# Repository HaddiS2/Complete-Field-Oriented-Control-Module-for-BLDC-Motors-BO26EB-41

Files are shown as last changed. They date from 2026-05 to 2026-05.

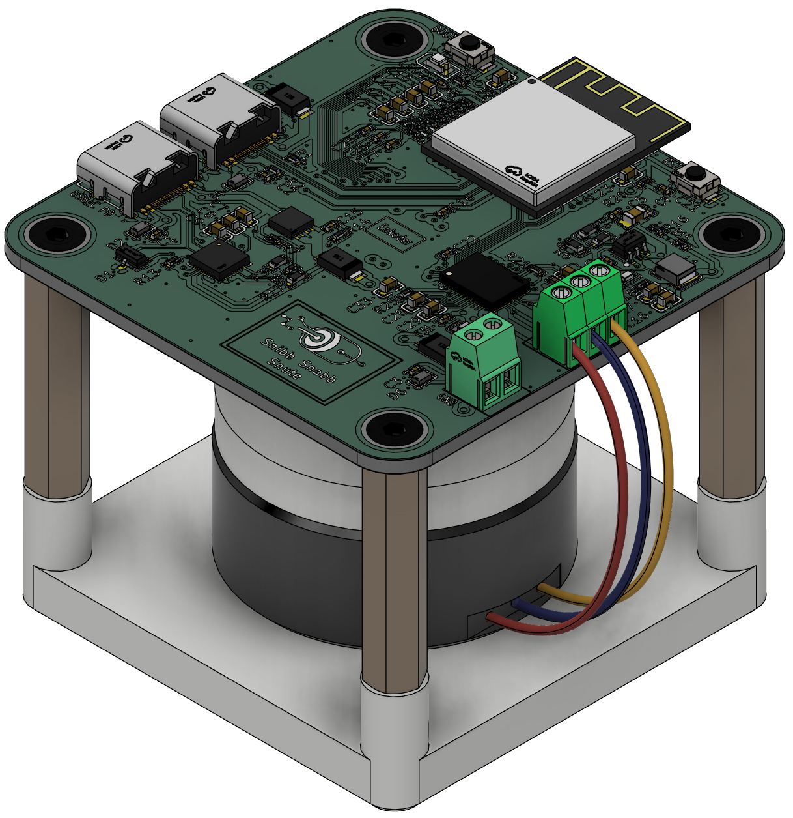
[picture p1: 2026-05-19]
CAD/FOC_Motor_Rig_Top_View.png

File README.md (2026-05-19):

# Complete-Field-Oriented-Control-Module-for-BLDC-Motors-BO26EB-41
Custom field-oriented control (FOC) motor controller with USB-C Power Delivery.

This repository contains the hardware design files, firmware, and test rig for a custom brushless motor controller built around field-oriented control (FOC). The board negotiates its supply voltage over USB-C Power Delivery using an STUSB4500, and measures rotor position with a TLE5009 magnetic encoder mounted directly beneath the motor shaft. The PCB was designed in KiCad, and a custom test rig — modeled in Fusion 360 and 3D printed — holds the motor and controller in fixed alignment to keep the encoder-to-magnet spacing constant for repeatable position- and velocity-control testing.

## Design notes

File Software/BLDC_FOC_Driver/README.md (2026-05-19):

# BLDC FOC Driver 
 
Motor controller based on Field Oriented Control (FOC). 
 
## Required Libraries: 
- **SimpleFOC** - Install via Arduino Library Manager 
- **SparkFun_STUSB4500** - Install via Arduino Library Manager (if needed) 
 
## Installation: 
1. Open Arduino IDE 
2. Go to **Sketch  Include Library  Manage Libraries** 
3. Search for "SimpleFOC" and install 
4. Search for "SparkFun STUSB4500" and install

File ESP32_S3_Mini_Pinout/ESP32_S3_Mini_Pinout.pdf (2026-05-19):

## ESP-32 S3 mini pin out diagram

Pin number | IO number | Pin type | Pin connection | description
1 | GND | GND | GND
2 | GND | GND | GND
3 | 3v3 | 3v3 | Powersupply3v3
4 | IO00 STRAPPING PIN | | Boot
5 | IO01 | ADC | Vref
6 | IO02 | ADC | ENK_Vgmr
7 | IO03 STRAPPING PIN | | -
8 | IO04 | ADC | ENK_SINN
9 | IO05 | ADC | ENK_SINP
10 | IO06 | ADC | ENK_COSP
11 | IO07 | ADC | ENK_COSN
12 | IO08 | ADC | SOA
13 | IO09 | ADC | SOB
14 | IO10 | ADC | SOC
15 | IO11 | IO | PWM_LC
16 | IO12 | IO | PWM_HC
17 | IO13 | IO | PWM_LB
18 | IO14 | IO | PWM_HB
19 | IO15 | IO | PWM_LA
20 | IO16 | IO | PWM_HA
21 | IO17 | I2C | SDA
22 | IO18 | I2C | SCL
23 | IO19 | D- | USB_C data | -
24 | IO20 | D+ | USB_C data | +
25 | IO21 | IO | RST_PDA
26 | IO26b | NC | -
27 | IO47 | SDA | SPICLK_P_DIFF
28 | IO33 | SPI/IO4 | SPI_nSCS
29 | IO34 | SPI/IO4 | SPI_SCLK
30 | IO48 | SDA | SPICLK_N_DIFF
31 | IO35 | SPI/IO6 | SPI_SDI
32 | IO36 | SPI/IO7 | SPI_SDO
33 | IO37 | SPI/IO | nSLEEP
34 | IO38 | IO | nFAULT
35 | IO39 | JTAG/IO | DRVOFF
36 | IO40 | JTAG | NC
37 | IO41 | JTAG | NC
38 | IO42 | JTAG | NC
39 | TXD0 | RTXDO | NC
40 | RXT0 | RXDO | NC
41 | IO45 STRAPPING PIN | | NC
44 | IO46 STRAPPING PIN | | NC
45 | EN | EN | NC
42,43,46,47,48 | - | GND | GND

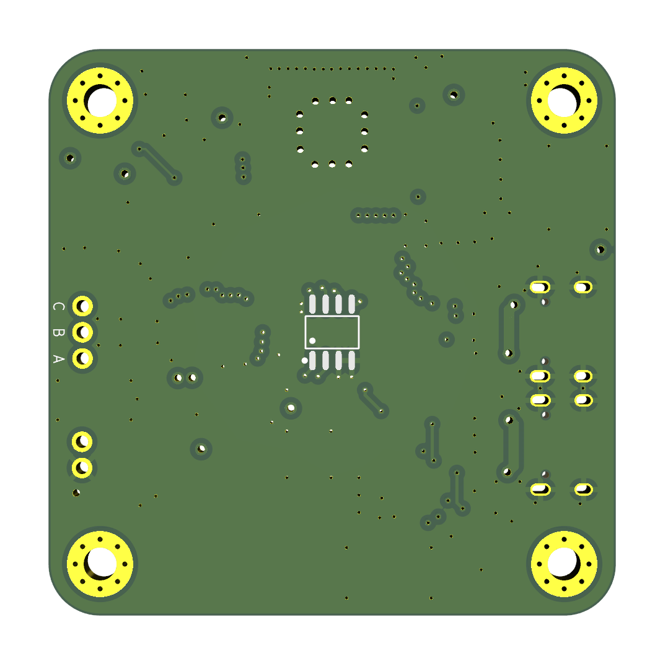
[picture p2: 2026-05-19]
Hardware/PCB_BackCompressed.png

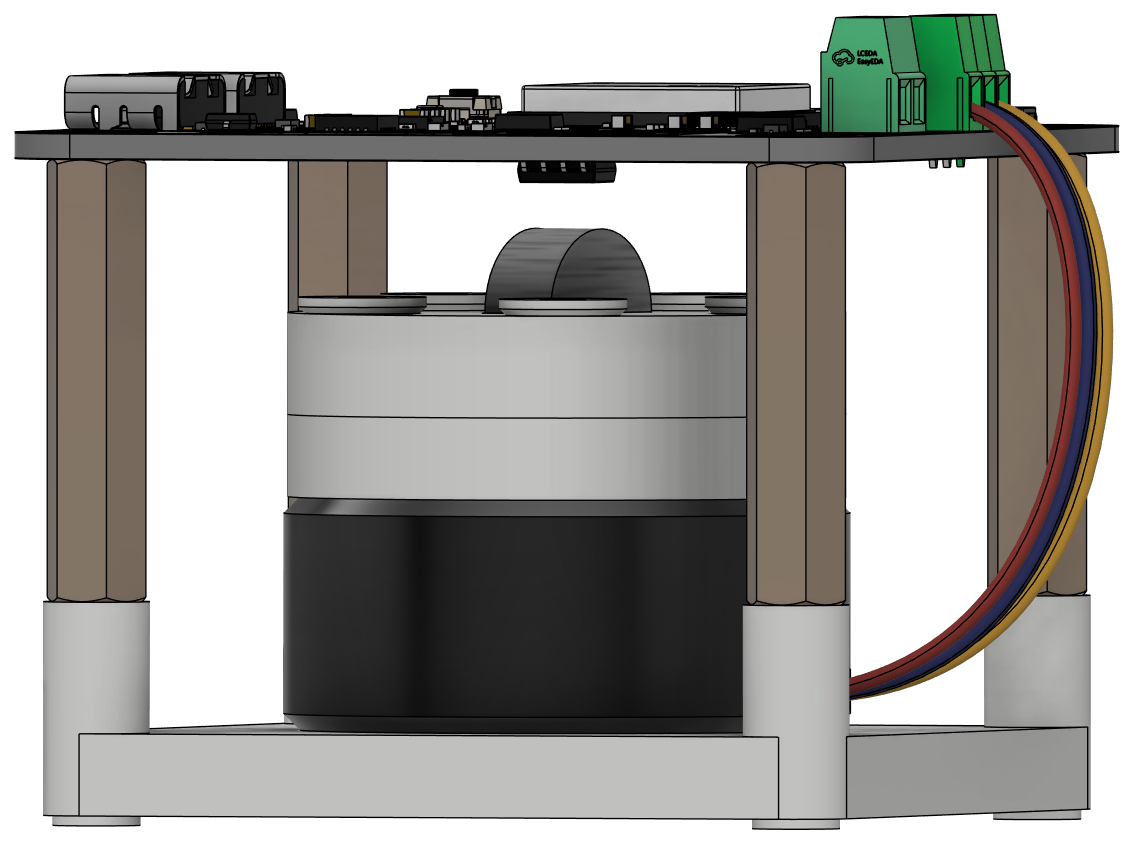
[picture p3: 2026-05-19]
CAD/FOC_Motor_Rig_Side_View.png

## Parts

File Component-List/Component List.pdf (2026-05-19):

1

# Component list for first iteration

Component | Description | Quantity | Electrical Specification | Size [SMD] | LCSC part# | Name | Component Link | Datasheet Link | Price x Qty Capacitor | CVM1/MCU_V | x10 | 100nF 50V X7R ±10% | 0603 | C14663 | CC0603KRX7R9BB104 | C14663 | C14663 | $0.0026 x 1 Capacitor | CVM2/VIN | x2 | 10uF 50V X7R ±10 | 1206 | C89632 | CL31B106KBHNNNE | C89632 | C89632 | $0.0377 x 1 Capacitor | CCP/CAVVD/MCU_EN/2.7/1.2/VDD | x6 | 1uF 50V X7R ±10% | 0805 | C28323 | CL21B105KBFNNNE | C28323 | C28323 | $0.0099 x 1 Capacitor | MCU_V/SW_BK/3V3/3V3 | x4 | 22uF 25V X5R ±20% | 0805 | C45783 | CL21A226MAQNNNE | C45783 | C45783 | $0.0308 x 1 Capacitor | CSOX | x3 | 22pF 50V C0G ±5% | 0402 | C1555 | CL21A226MAQNNNE | C1555 | C1555 | $0.0012 x 1 Capacitor | CFLY | x1 | 47nF 50V X7R ±10% | 0603 | C1622 | CL10B473KB8NNNC | C1622 | C1622 | $0.0052 x 1 Capacitor | SINP/SINN/COSP/COSN | x4 | 68nF 50V C0G ±5% | 1206 | C77084 | GRM31C5C1H683JA01L | C77084 | C77084 | $0.1122 x 1 Capacitor | GMR/VDD/USBC/USBC_PD/DC | x5 | 4.7nF 50V X7R ±10% | 0603 | C1621 | CL10B472KB8NNNC | C1621 | C1621 | $0.0031 x 1 Resistor | RnFault | x1 | 5.1kΩ 50V 62.5mW Thick Film Resistor ±1% | 0402 | C105872 | RC0402FR-075K1L | C105872 | C105872 | $0.0006 x 1 Resistor | RBK/D+/D-/DIode blå-grønn | x3 | 22Ω 150V 125mW Thick Film Resistor ±1% | 0805 | C17561 | 0805W8F220JT5E | C17561 | C17561 | $0.0024 x 1 Resistor | RSOX/IO0 | x4 | 330Ω 150V 125mW Thick Film Resistor ±1% | 0805 | C17630 | 0805W8F3300T5E | C17630 | C17630 | $0.0022 x 1 Resistor | G/FB/RESET | x3 | 100kΩ 150V 125mW thick Film Resistor ±1% | 0805 | C149504 | 0805W8F1003T5E | C149504 | C149504 | $0.0023 x 1 Resistor | Enable, SINP/N, COSP/N | x5 | 10kΩ 75V 100mW Thick Film Resistor ±1% | 0603 | C2906982 | FRC0603F1002TS | C2906982 | C2906982 | $0.0007 x 1 Resistor | FB/G | x2 | 22kΩ 150V 125mW Thick Film Resistor ±1% | 0805 | C17560 | 0805W8F2202T5E | C17560 | C17560 | $0.0022 x 1 Resistor | VBUS_DISCH/DISCH | x2 | 1kΩ 150V 125mW Thick Film Resistor ±1% | 0805 | C95781 | RC0805FR-071KL | C95781 | C95781 | $0.0015 x 1 Resistor | EN | x1 | 220kΩ 150V 125mW Thick Film Resistor ±1% | 0805 | C17556 | 0805W8F2203T5E | C17556 | C17556 | $0.0022 x 1 Resistor | Rød LED | x1 | 75Ω 100mW 75V Thick Film Resistor ±1% | 0603 | C4275 | 0603WAF750JT5E | C4275 | C4275 | $0.0015 x 1 Resistor | EN | x1 | 560kΩ 125mW 150V Thick Film Resistor ±1% | 0805 | C15785 | 0805W8F5603T5E | C15785 | C15785 | $0.0021 x 1
Inductor | BOOT | x1 | 10uH 2A | 1210 | C39846661 | XRTC322512S100MBCA | C39846661 (https://jlcpcb.com/partdetail/XR-XRTC322512S100MBCA/C39846661) | C39846661 (https://www.lcsc.com/datasheet/C39846661.pdf) | $0.1224 x 1
LED | Red | x1 | 2.4V 20mA 40mW 615nm~630nm | 0603 | C2286 | KT-0603R | C2286 (https://jlcpcb.com/partdetail/Hubei_KENTOElec-KT0603R/C2286) | C2286 (https://jlcpcb.com/api/file/downloadByFileSystemAccessId/8550723991833485312) | $0.0064 x 1
LED | Green | x1 | 2.6V~3.1V 5mA 100mW 513nm~528nm | 0805 | C2297 | KT-0805G | C2297 (https://jlcpcb.com/parts/2nd/Optoelectronics/LED_Indication_Discrete_71) | C2297 (https://jlcpcb.com/api/file/downloadByFileSystemAccessId/8639582106239348736) | $0.0157 x 1 Connector | DC power | x1 | 2 Position Wire to Board Terminal Block | Through Hole 5.08mm | C8465 | KANGNEX WJ500V-5.08-2P | C8465 | C8465 | $0.1281 x 1 Connector | OUTPUT | x1 | 3 Position Wire to Board Terminal Block | Through Hole 5.08mm | C430602 | DB128L-5.08-3P-BK-S | C430602 | C430602 | $0.2321 x 1 Connector | USB-C Connector | x2 | 20V 5A -30℃~+80℃ | 8.94mmx7.35mmx3.26mm | C165948 | TYPE-C-31-M-12 | C165948 | C165948 | $0.1810 x 1
Switch | EN, BOOT | x2 | Black Round Button SMD | 4mmx3mmx2mm | C720477 | TS-1088-AR02016 | C720477 (https://jlcpcb.com/partdetail/XUNPU-TS_1088AR02016/C720477) | C720477 (https://jlcpcb.com/api/file/downloadByFileSystemAccessId/8588886944068096000) | $0.0555 x 1
IC | USB-C PD | x1 | 3V;5.5V 160uA -40℃~+105℃ | 2.6mmx2.6mmx0.5mm | C2678061 | STUSB4500QTR | C2678061 (https://www.lcsc.com/product-detail/C2678061.html?s_z=n_STUSB4500) | C2678061 (https://www.lcsc.com/datasheet/C2678061.pdf) | $1.3770 x 1
IC | Encoder | x1 | 3V~3.6V 7mA -40℃~+150℃ | 5mmx6mmx1.75mm | C2655191 | TLE5009E1000FUMA1 | C2655191 (https://www.lcsc.com/product-detail/C2655191.html?s_z=n_TLE5009E1000FUMA1%2520) | C2655191 (https://www.lcsc.com/datasheet/C2655191.pdf) | $3.7725 x 1
IC | Microcontroller | x1 | 2.4GHz 3V~3.6V 97mA -40℃~+85℃ | 20.5mmx15.4mmx2.4mm | C2913206 | ESP32-S3-MINI-1-N8 | C2913206 (https://www.lcsc.com/product-detail/C2913206.html?s_z=n_esp32-s3%2520wroom%25201) | C2913206 (https://www.lcsc.com/datasheet/C2913206.pdf) | $4.5968 x 1
IC | Motor driver | x1 | 4.5-35V 8A peak 200-kHz PWM -40℃~+125℃ | 5mmx7mmx1mm | C20345369 | DRV8316CRQRGFRQ1 | C20345369 (https://jlcpcb.com/partdetail/TexasInstruments-DRV8316CRQRGFRQ1/C20345369) | C20345369 (https://jlcpcb.com/api/file/downloadByFileSystemAccessId/8590902495441076224) | $6.6228 x 1
IC | Power mosfet for power switching Voltage regulator | x1 x1 | 500kHz Buck Adjustable 2A 4.5V~28V 30V 40A | 3.15mmx3.3mmx0.75mm 1.6mmx2.9mmx1mm | C49452333 C191884 | TPS54202DDCR STL9P3LLH6-TP | C49452333 C191884 (https://www.lcsc.com/product-detail/C191884.html?s_z=n_TPS54202) | C49452333 C191884 (https://www.lcsc.com/datasheet/C191884.pdf) | $0.2030 x 1 Mosfet $0.1990 x 1
Diode | VCC buss diode | x3 | 30V 5A | 5mmx2.7mmx1mm | C50603 | PMEG3050EP,115 | C50603 (https://www.lcsc.com/product-detail/C50603.html?s_z=n_PMEG3050EP) | C50603 (https://www.lcsc.com/datasheet/C50603.pdf) | $0.4075 x 1 Diode | ESD Diode | x1 | 25VC Clamp ESD DIODE | 1.6mmx3mmx1.4mm | C95343 | ESDA25L | C95343 | C95343 | $0.0826 x 1 Diode | ESD Diode | x3 | 38VC Clamp ESD DIODE | 1.6mmx1mmx0.5mm | C19829649 | ESDA25P35-1U1M | C19829649 | C19829649 | $0.1098 x 1
Pin | Header pin | x12 | 3A 250V 2xpin header | 3mm 2.54mm | C492401 | PZ254V-11-02P | C492401 (https://www.lcsc.com/product-detail/C492401.html?s_z=n_C492401) | C492401 (https://www.lcsc.com/datasheet/C492401.pdf) | $0.0084

2

# Component list for second iteration

Component | Description | Quantity | Electrical Specification | Size [SMD] | LCSC part# | Name | Component Link | Datasheet Link | Price x Qty Capacitor | CSOX | x3 | 22pF 50V C0G ±5% | 0402 | C1555 | 0402CG220J500NT | C1555 | C1555 | $0.0014 x 1 Capacitor | GMR/USBC/USBC_PD/DC | x4 | 4.7nF 50V X7R ±10% | 0402 | C1538 | 0402B472K500NT | C1538 | C1538 | $ 0.0013 x 1 Capacitor | SINP/SINN/COSP/COSN/CFLY | x5 | 47nF 50V X7R ±10% | 0603 | C1622 | CL10B473KB8NNNC | C1622 | C1622 | $0.0057 x 1 Capacitor | BOOT/VMCU/VCC/3V3/nFAULT/VDD | x9 | 100nF 50V X7R ±10% | 0402 | C307331 | CL05B104KB54PNC | C307331 | C307331 | $ 0.0047 x 1 Capacitor | CCP/CAVVD/MCU_EN/2.7/1.2/VDD | x6 | 1uF 50V X5R ±10% | 0603 | C15849 | CL10A105KB8NNNC | C15849 | C15849 | $ 0.0077 x 1 Capacitor | CVM2/VIN | x2 | 10uF 50V X5R ±10% | 0805 | C440198 | GRM21BR61H106KE43L | C440198 | C440198 | $ 0.0687 x 1 Capacitor | MCU_V/SW_BK/3V3/3V3 | x4 | 22uF 6.3V X5R ±20% | 0603 | C59461 | CL10A226MQ8NRNC | C59461 | C59461 | $ 0.0101 x 1 Resistor | SW_BK | x1 | 22Ω 62.5mW Thick Film Resistor ±1% | 0402 | C25092 | 0402WGF220JTCE | C25092 | C25092 | $ 0.0009 x 1 Resistor | MFET_FB/RED_DIODE | x2 | 100Ω 62.5mW Thick Film Resistor ±1% | 0402 | C25076 | 0402WGF1000TCE | C25076 | C25076 | $ 0.0010 x 1 Resistor | RSOX/IO0 | x4 | 330Ω 62.5mW Thick Film Resistor ±1% | 0402 | C25104 | 0402WGF3300TCE | C25104 | C25104 | $ 0.0011 x 1 Resistor | VBUS_DISCH/DISCH | x2 | 1kΩ 100mW Thick Film Resistor ±1% | 0603 | C21190 | 0603WAF1001T5E | C21190 | C21190 | $ 0.0016 x 1 Resistor | C+/C-/RnFAULT | x3 | 5.1kΩ 62.5mW Thick Film Resistor ±1% | 0402 | C25905 | 0402WGF5101TCE | C25905 | C25905 | $ 0.0009 x 1 Resistor | MCU_Reset / SINP/N / COSP/N | x5 | 10kΩ 62.5mW Thick Film Resistor ±1% | 0402 | C25744 | 0402WGF1002TCE | C25744 | C25744 | $ 0.0013 x 1 Resistor | MFET_GATE/3V3_FB | x2 | 22kΩ 62.5mW Thick Film Resistor ±1% | 0402 | C25768 | 0402WGF2202TCE | C25768 | C25768 | $ 0.0010 x 1 Resistor | MFET_GATE/3V3_FB/STUSB_Reset | x3 | 100kΩ 62.5mW Thick Film Resistor ±1% | 0402 | C25741 | 0402WGF1003TCE | C25741 | C25741 | $ 0.0009 x 1 Resistor | 3V3_Enable | x1 | 220kΩ 100mW Thick Film Resistor ±1% | 0603 | C22961 | 0603WAF2203T5E | C22961 | C22961 | $ 0.0014 x 1 Resistor | 3V3_Enable | x1 | 510kΩ 100mW Thick Film Resistor ±1% | 0603 | C23192 | 0603WAF5103T5E | C23192 | C23192 | $ 0.0019 x 1 Resistor | 3V3_Enable | x1 | 56kΩ 100mW Thick Film Resistor ±1% | 0603 | C23206 | 0603WAF5602T5E | C23206 | C23206 | $ 0.0016 x 1
Inductor | BOOT | x1 | 10uH 2A | 1210 | C39846661 | XRTC322512S100MBCA | C39846661 (https://jlcpcb.com/partdetail/XR-XRTC322512S100MBCA/C39846661) | C39846661 (https://www.lcsc.com/datasheet/C39846661.pdf) | $0.1224 x 1
LED | Rød | x1 | 2.4V 20mA 40mW 615nm~630nm | 0603 | C2286 | KT-0603R | C2286 (https://jlcpcb.com/partdetail/Hubei_KENTOElec-KT0603R/C2286) | C2286 (https://jlcpcb.com/api/file/downloadByFileSystemAccessId/8550723991833485312) | $0.0064 x 1
LED | Grønn | x1 | 2.6V~3.1V 5mA 100mW 513nm~528nm | 0805 | C2297 | KT-0805G | C2297 (https://jlcpcb.com/parts/2nd/Optoelectronics/LED_Indication_Discrete_71) | C2297 (https://jlcpcb.com/api/file/downloadByFileSystemAccessId/8639582106239348736) | $0.0157 x 1 Connector | USB-C Connector | x2 | 20V 5A -30℃~+80℃ | 8.94mmx7.35mmx3.26mm | C165948 | TYPE-C-31-M-12 | C165948 | C165948 | $0.1810 x 1 Connector | OUTPUT | x1 | 3 Position Wire to Board Terminal Block | Through Hole 2.54mm | C49291873 | C254128V-3P0G36 | C49291873 | C49291873 | $ 0.3968 x 1 Connector | DC power | x1 | 2 Position Wire to Board Terminal Block | Through Hole 2.54mm | C49291872 | C254128V-2P0G36 | C49291872 | C49291872 | $ 0.2661 x 1
Switch | EN, BOOT | x2 | Black Round Button SMD | 4mmx3mmx2mm | C720477 | TS-1088-AR02016 | C720477 (https://jlcpcb.com/partdetail/XUNPU-TS_1088AR02016/C720477) | C720477 (https://jlcpcb.com/api/file/downloadByFileSystemAccessId/8588886944068096000) | $0.0555 x 1
IC | USB-C PD | x1 | 3V;5.5V 160uA -40℃~+105℃ | 2.6mmx2.6mmx0.5mm | C2678061 | STUSB4500QTR | C2678061 (https://www.lcsc.com/product-detail/C2678061.html?s_z=n_STUSB4500) | C2678061 (https://www.lcsc.com/datasheet/C2678061.pdf) | $1.3770 x 1
IC | Encoder | x1 | 3V~3.6V 7mA -40℃~+150℃ | 5mmx6mmx1.75mm | C2655191 | TLE5009E1000FUMA1 | C2655191 (https://www.lcsc.com/product-detail/C2655191.html?s_z=n_TLE5009E1000FUMA1%2520) | C2655191 (https://www.lcsc.com/datasheet/C2655191.pdf) | $3.7725 x 1
IC | Microcontroller | x1 | 2.4GHz 3V~3.6V 97mA -40℃~+85℃ | 20.5mmx15.4mmx2.4mm | C2913206 | ESP32-S3-MINI-1-N8 | C2913206 (https://www.lcsc.com/product-detail/C2913206.html?s_z=n_esp32-s3%2520wroom%25201) | C2913206 (https://www.lcsc.com/datasheet/C2913206.pdf) | $4.5968 x 1
IC | Motor driver | x1 | 4.5-35V 8A peak 200-kHz PWM -40℃~+125℃ | 5mmx7mmx1mm | C20345369 | DRV8316CRQRGFRQ1 | C20345369 (https://jlcpcb.com/partdetail/TexasInstruments-DRV8316CRQRGFRQ1/C20345369) | C20345369 (https://jlcpcb.com/api/file/downloadByFileSystemAccessId/8590902495441076224) | $6.6228 x 1
IC | Voltage regulator | x1 | 500kHz Buck Adjustable 2A 4.5V~28V | 1.6mmx2.9mmx1mm | C191884 | TPS54202DDCR | C191884 (https://www.lcsc.com/product-detail/C191884.html?s_z=n_TPS54202) | C191884 (https://www.lcsc.com/datasheet/C191884.pdf) | $0.2030 x 1 Mosfet | Power mosfet for power switching | x1 | 30V 40A | 3.15mmx3.3mmx0.75mm | C49452333 | STL9P3LLH6-TP | C49452333 | C49452333 | $0.1990 x 1 Diode | VCC buss diode | x3 | 30V 5A | 5mmx2.7mmx1mm | C50603 | PMEG3050EP,115 | C50603 | C50603 | $0.4075 x 1 Diode | ESD Diode | x1 | 25VC Clamp ESD DIODE | 1.6mmx3mmx1.4mm | C95343 | ESDA25L | C95343 | C95343 | $0.0826 x 1 Diode | ESD Diode | x3 | 38VC Clamp ESD DIODE | 1.6mmx1mmx0.5mm | C19829649 | ESDA25P35-1U1M | C19829649 | C19829649 | $0.1098 x 1

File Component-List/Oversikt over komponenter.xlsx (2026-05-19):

Component list for first iteration
Component | Description | Quantity | Electrical Specification | Size [SMD] | LCSC part# | Name | Component Link | Datasheet Link | Price x Qty
Capacitor | CVM1/MCU_V | x10 | 100nF 50V X7R ±10% | 0603 | C14663 | CC0603KRX7R9BB104 | C14663 (https://www.lcsc.com/product-detail/C14663.html) | C14663 (https://www.lcsc.com/datasheet/C162178.pdf) | $0.0026 x 1
Capacitor | CVM2/VIN | x2 | 10uF 50V X7R ±10 | 1206 | C89632 | CL31B106KBHNNNE | C89632 (https://www.lcsc.com/product-detail/C89632.html?s_z=n_C89632) | C89632 (https://www.lcsc.com/datasheet/C89632.pdf) | $0.0377 x 1
Capacitor | CCP/CAVVD/MCU_EN/2.7/1.2/VDD | x6 | 1uF 50V X7R ±10% | 0805 | C28323 | CL21B105KBFNNNE | C28323 (https://www.lcsc.com/product-detail/C28323.html?s_z=n_C28323) | C28323 (https://www.lcsc.com/datasheet/C28323.pdf) | $0.0099 x 1
Capacitor | MCU_V/SW_BK/3V3/3V3 | x4 | 22uF 25V X5R ±20% | 0805 | C45783 | CL21A226MAQNNNE | C45783 (https://www.lcsc.com/product-detail/C45783.html?s_z=n_C45783) | C45783 (https://www.lcsc.com/datasheet/C45783.pdf) | $0.0308 x 1
Capacitor | CSOX | x3 | 22pF 50V C0G ±5% | 0402 | C1555 | CL21A226MAQNNNE | C1555 (https://www.lcsc.com/product-detail/C1555.html?s_z=n_%2520C1555) | C1555 (https://www.lcsc.com/datasheet/C1555.pdf) | $0.0012 x 1
Capacitor | CFLY | x1 | 47nF 50V X7R ±10% | 0603 | C1622 | CL10B473KB8NNNC | C1622 (https://jlcpcb.com/partdetail/1974-CL10B473KB8NNNC/C1622) | C1622 (https://jlcpcb.com/api/file/downloadByFileSystemAccessId/8579707009123745792) | $0.0052 x 1
Capacitor | SINP/SINN/COSP/COSN | x4 | 68nF 50V C0G ±5% | 1206 | C77084 | GRM31C5C1H683JA01L | C77084 (https://www.lcsc.com/product-detail/C77084.html?s_z=n_capasitor%252068n) | C77084 (https://www.lcsc.com/datasheet/C77084.pdf) | $0.1122 x 1
Capacitor | GMR/VDD/USBC/USBC_PD/DC | x5 | 4.7nF 50V X7R ±10% | 0603 | C1621 | CL10B472KB8NNNC | C1621 (https://www.lcsc.com/product-detail/C1621.html?s_z=n_C1621) | C1621 (https://www.lcsc.com/datasheet/C1621.pdf) | $0.0031 x 1
Resistor | RnFault | x1 | 5.1kΩ 50V 62.5mW Thick Film Resistor ±1% | 0402 | C105872 | RC0402FR-075K1L | C105872 (https://www.lcsc.com/product-detail/C105872.html?s_z=n_C105872) | C105872 (https://www.lcsc.com/datasheet/C105872.pdf) | $0.0006 x 1
Resistor | RBK/D+/D-/DIode blå-grønn | x3 | 22Ω 150V 125mW Thick Film Resistor ±1% | 0805 | C17561 | 0805W8F220JT5E | C17561 (https://jlcpcb.com/partdetail/18249-0805W8F220JT5E/C17561) | C17561 (https://jlcpcb.com/api/file/downloadByFileSystemAccessId/8579706537314738176) | $0.0024 x 1
Resistor | RSOX/IO0 | x4 | 330Ω 150V 125mW Thick Film Resistor ±1% | 0805 | C17630 | 0805W8F3300T5E | C17630 (https://jlcpcb.com/partdetail/18318-0805W8F3300T5E/C17630) | C17630 (https://jlcpcb.com/api/file/downloadByFileSystemAccessId/8579706569889464320) | $0.0022 x 1
Resistor | G/FB/RESET | x3 | 100kΩ 150V 125mW thick Film Resistor ±1% | 0805 | C149504 | 0805W8F1003T5E | C149504 (https://jlcpcb.com/parts/basic_parts) | C149504 (https://jlcpcb.com/api/file/downloadByFileSystemAccessId/8588884762697584640) | $0.0023 x 1
Resistor | Enable, SINP/N, COSP/N | x5 | 10kΩ 75V 100mW Thick Film Resistor ±1% | 0603 | C2906982 | FRC0603F1002TS | C2906982 (https://www.lcsc.com/product-detail/C2906982.html?s_z=n_C2906982) | C2906982 (https://www.lcsc.com/datasheet/C2906982.pdf) | $0.0007 x 1
Resistor | FB/G | x2 | 22kΩ 150V 125mW Thick Film Resistor ±1% | 0805 | C17560 | 0805W8F2202T5E | C17560 (https://jlcpcb.com/partdetail/18248-0805W8F2202T5E/C17560) | C17560 (https://jlcpcb.com/api/file/downloadByFileSystemAccessId/8579706534533644288) | $0.0022 x 1
Resistor | VBUS_DISCH/DISCH | x2 | 1kΩ 150V 125mW Thick Film Resistor ±1% | 0805 | C95781 | RC0805FR-071KL | C95781 (https://www.lcsc.com/product-detail/C95781.html?s_z=n_C95781) | C95781 (https://jlcpcb.com/api/file/downloadByFileSystemAccessId/8579706499683172352) | $0.0015 x 1
Resistor | EN | x1 | 220kΩ 150V 125mW Thick Film Resistor ±1% | 0805 | C17556 | 0805W8F2203T5E | C17556 (https://jlcpcb.com/partdetail/18244-0805W8F2203T5E/C17556) | C17556 (https://jlcpcb.com/api/file/downloadByFileSystemAccessId/8579706528460427264) | $0.0022 x 1
Resistor | Rød LED | x1 | 75Ω 100mW 75V Thick Film Resistor ±1% | 0603 | C4275 | 0603WAF750JT5E | C4275 (https://jlcpcb.com/parts/2nd/Resistors/Chip_Resistor_Surface_Mount_2980) | C4275 (https://jlcpcb.com/api/file/downloadByFileSystemAccessId/8579706081771380736) | $0.0015 x 1
Resistor | EN | x1 | 560kΩ 125mW 150V Thick Film Resistor ±1% | 0805 | C15785 | 0805W8F5603T5E | C15785 (https://jlcpcb.com/partdetail/16467-0805W8F5603T5E/C15785) | C15785 (https://jlcpcb.com/api/file/downloadByFileSystemAccessId/8579706452040617984) | $0.0021 x 1
Inductor | BOOT | x1 | 10uH 2A | 1210 | C39846661 | XRTC322512S100MBCA | C39846661 (https://jlcpcb.com/partdetail/XR-XRTC322512S100MBCA/C39846661) | C39846661 (https://www.lcsc.com/datasheet/C39846661.pdf) | $0.1224 x 1
LED | Red | x1 | 2.4V 20mA 40mW 615nm~630nm | 0603 | C2286 | KT-0603R | C2286 (https://jlcpcb.com/partdetail/Hubei_KENTOElec-KT0603R/C2286) | C2286 (https://jlcpcb.com/api/file/downloadByFileSystemAccessId/8550723991833485312) | $0.0064 x 1
LED | Green | x1 | 2.6V~3.1V 5mA 100mW 513nm~528nm | 0805 | C2297 | KT-0805G | C2297 (https://jlcpcb.com/parts/2nd/Optoelectronics/LED_Indication_Discrete_71) | C2297 (https://jlcpcb.com/api/file/downloadByFileSystemAccessId/8639582106239348736) | $0.0157 x 1
Connector | DC power | x1 | 2 Position Wire to Board Terminal Block | Through Hole 5.08mm | C8465 | KANGNEX WJ500V-5.08-2P | C8465 (https://www.lcsc.com/product-detail/C8465.html) | C8465 (https://www.lcsc.com/datasheet/C8465.pdf) | $0.1281 x 1
Connector | OUTPUT | x1 | 3 Position Wire to Board Terminal Block | Through Hole 5.08mm | C430602 | DB128L-5.08-3P-BK-S | C430602 (https://www.lcsc.com/product-detail/C72334.html) | C430602 (https://www.lcsc.com/datasheet/C72334.pdf) | $0.2321 x 1
Connector | USB-C Connector | x2 | 20V 5A -30℃~+80℃ | 8.94mmx7.35mmx3.26mm | C165948 | TYPE-C-31-M-12 | C165948 (https://www.lcsc.com/product-detail/C165948.html?s_z=n_USB-C%2520connector) | C165948 (https://www.lcsc.com/datasheet/C165948.pdf) | $0.1810 x 1
Switch | EN, BOOT | x2 | Black Round Button SMD | 4mmx3mmx2mm | C720477 | TS-1088-AR02016 | C720477 (https://jlcpcb.com/partdetail/XUNPU-TS_1088AR02016/C720477) | C720477 (https://jlcpcb.com/api/file/downloadByFileSystemAccessId/8588886944068096000) | $0.0555 x 1
IC | USB-C PD | x1 | 3V;5.5V 160uA -40℃~+105℃ | 2.6mmx2.6mmx0.5mm | C2678061 | STUSB4500QTR | C2678061 (https://www.lcsc.com/product-detail/C2678061.html?s_z=n_STUSB4500) | C2678061 (https://www.lcsc.com/datasheet/C2678061.pdf) | $1.3770 x 1
IC | Encoder | x1 | 3V~3.6V 7mA -40℃~+150℃ | 5mmx6mmx1.75mm | C2655191 | TLE5009E1000FUMA1 | C2655191 (https://www.lcsc.com/product-detail/C2655191.html?s_z=n_TLE5009E1000FUMA1%2520) | C2655191 (https://www.lcsc.com/datasheet/C2655191.pdf) | $3.7725 x 1
IC | Microcontroller | x1 | 2.4GHz 3V~3.6V 97mA -40℃~+85℃ | 20.5mmx15.4mmx2.4mm | C2913206 | ESP32-S3-MINI-1-N8 | C2913206 (https://www.lcsc.com/product-detail/C2913206.html?s_z=n_esp32-s3%2520wroom%25201) | C2913206 (https://www.lcsc.com/datasheet/C2913206.pdf) | $4.5968 x 1
IC | Motor driver | x1 | 4.5-35V 8A peak 200-kHz PWM -40℃~+125℃ | 5mmx7mmx1mm | C20345369 | DRV8316CRQRGFRQ1 | C20345369 (https://jlcpcb.com/partdetail/TexasInstruments-DRV8316CRQRGFRQ1/C20345369) | C20345369 (https://jlcpcb.com/api/file/downloadByFileSystemAccessId/8590902495441076224) | $6.6228 x 1
IC | Voltage regulator | x1 | 500kHz Buck Adjustable 2A 4.5V~28V | 1.6mmx2.9mmx1mm | C191884 | TPS54202DDCR | C191884 (https://www.lcsc.com/product-detail/C191884.html?s_z=n_TPS54202) | C191884 (https://www.lcsc.com/datasheet/C191884.pdf) | $0.2030 x 1
Mosfet | Power mosfet for power switching | x1 | 30V 40A | 3.15mmx3.3mmx0.75mm | C49452333 | STL9P3LLH6-TP | C49452333 (https://www.lcsc.com/product-detail/C49452333.html?s_z=n_STL9P3LLH6) | C49452333 (https://www.lcsc.com/datasheet/C49452333.pdf) | $0.1990 x 1
Diode | VCC buss diode | x3 | 30V 5A | 5mmx2.7mmx1mm | C50603 | PMEG3050EP,115 | C50603 (https://www.lcsc.com/product-detail/C50603.html?s_z=n_PMEG3050EP) | C50603 (https://www.lcsc.com/datasheet/C50603.pdf) | $0.4075 x 1
Diode | ESD Diode | x1 | 25VC Clamp ESD DIODE | 1.6mmx3mmx1.4mm | C95343 | ESDA25L | C95343 (https://www.lcsc.com/product-detail/C95343.html?s_z=n_ESDA25L) | C95343 (https://www.lcsc.com/datasheet/C95343.pdf) | $0.0826 x 1
Diode | ESD Diode | x3 | 38VC Clamp ESD DIODE | 1.6mmx1mmx0.5mm | C19829649 | ESDA25P35-1U1M | C19829649 (https://www.lcsc.com/product-detail/C19829649.html?s_z=n_ESDA25P35) | C19829649 (https://www.lcsc.com/datasheet/C19829649.pdf) | $0.1098 x 1
Pin | Header pin | x12 | 3A 250V 2xpin header | 3mm 2.54mm | C492401 | PZ254V-11-02P | C492401 (https://www.lcsc.com/product-detail/C492401.html?s_z=n_C492401) | C492401 (https://www.lcsc.com/datasheet/C492401.pdf) | $0.0084
Component list for second iteration
Component | Description | Quantity | Electrical Specification | Size [SMD] | LCSC part# | Name | Component Link | Datasheet Link | Price x Qty
Capacitor | CSOX | x3 | 22pF 50V C0G ±5% | 0402 | C1555 | 0402CG220J500NT | C1555 (https://www.lcsc.com/product-detail/C1555.html?s_z=n_q_0402CG220J500NT) | C1555 (https://www.lcsc.com/datasheet/C1555.pdf) | $0.0014 x 1
Capacitor | GMR/USBC/USBC_PD/DC | x4 | 4.7nF 50V X7R ±10% | 0402 | C1538 | 0402B472K500NT | C1538 (https://www.lcsc.com/product-detail/C1538.html?s_z=n_q_0402B472K500NT) | C1538 (https://www.lcsc.com/datasheet/C1538.pdf) | $ 0.0013 x 1
Capacitor | SINP/SINN/COSP/COSN/CFLY | x5 | 47nF 50V X7R ±10% | 0603 | C1622 | CL10B473KB8NNNC | C1622 (https://www.lcsc.com/product-detail/C1622.html?s_z=n_q_CL10B473KB8NNNC) | C1622 (https://www.lcsc.com/datasheet/C1622.pdf) | $0.0057 x 1
Capacitor | BOOT/VMCU/VCC/3V3/nFAULT/VDD | x9 | 100nF 50V X7R ±10% | 0402 | C307331 | CL05B104KB54PNC | C307331 (https://www.lcsc.com/product-detail/C307331.html?s_z=n_q_CL05B104KB54PNC) | C307331 (https://www.lcsc.com/datasheet/C307331.pdf) | $ 0.0047 x 1
Capacitor | CCP/CAVVD/MCU_EN/2.7/1.2/VDD | x6 | 1uF 50V X5R ±10% | 0603 | C15849 | CL10A105KB8NNNC | C15849 (https://www.lcsc.com/product-detail/C15849.html?s_z=n_q_CL10A105KB8NNNC) | C15849 (https://www.lcsc.com/datasheet/C15849.pdf) | $ 0.0077 x 1
Capacitor | CVM2/VIN | x2 | 10uF 50V X5R ±10% | 0805 | C440198 | GRM21BR61H106KE43L | C440198 (https://www.lcsc.com/product-detail/C440198.html?s_z=n_q_GRM21BR61H106KE43L) | C440198 (https://www.lcsc.com/datasheet/C440198.pdf) | $ 0.0687 x 1
Capacitor | MCU_V/SW_BK/3V3/3V3 | x4 | 22uF 6.3V X5R ±20% | 0603 | C59461 | CL10A226MQ8NRNC | C59461 (https://www.lcsc.com/product-detail/C59461.html?s_z=n_q_CL10A226MQ8NRNC) | C59461 (https://www.lcsc.com/datasheet/C59461.pdf) | $ 0.0101 x 1
Resistor | SW_BK | x1 | 22Ω 62.5mW Thick Film Resistor ±1% | 0402 | C25092 | 0402WGF220JTCE | C25092 (https://www.lcsc.com/product-detail/C25092.html?s_z=n_q_0402WGF220JTCE) | C25092 (https://www.lcsc.com/datasheet/C25092.pdf) | $ 0.0009 x 1
Resistor | MFET_FB/RED_DIODE | x2 | 100Ω 62.5mW Thick Film Resistor ±1% | 0402 | C25076 | 0402WGF1000TCE | C25076 (https://www.lcsc.com/product-detail/C25076.html?s_z=n_q_0402WGF1000TCE) | C25076 (https://www.lcsc.com/datasheet/C25076.pdf) | $ 0.0010 x 1
Resistor | RSOX/IO0 | x4 | 330Ω 62.5mW Thick Film Resistor ±1% | 0402 | C25104 | 0402WGF3300TCE | C25104 (https://www.lcsc.com/product-detail/C25104.html?s_z=n_q_0402WGF3300TCE) | C25104 (https://www.lcsc.com/datasheet/C25104.pdf) | $ 0.0011 x 1
Resistor | VBUS_DISCH/DISCH | x2 | 1kΩ 100mW Thick Film Resistor ±1% | 0603 | C21190 | 0603WAF1001T5E | C21190 (https://www.lcsc.com/product-detail/C21190.html?s_z=n_q_C21190&globalKeyword=C21190) | C21190 (https://www.lcsc.com/datasheet/C21190.pdf) | $ 0.0016 x 1
Resistor | C+/C-/RnFAULT | x3 | 5.1kΩ 62.5mW Thick Film Resistor ±1% | 0402 | C25905 | 0402WGF5101TCE | C25905 (https://www.lcsc.com/product-detail/C25905.html?s_z=n_q_C25905&globalKeyword=C25905) | C25905 (https://www.lcsc.com/datasheet/C25905.pdf) | $ 0.0009 x 1
Resistor | MCU_Reset / SINP/N / COSP/N | x5 | 10kΩ 62.5mW Thick Film Resistor ±1% | 0402 | C25744 | 0402WGF1002TCE | C25744 (https://www.lcsc.com/product-detail/C25744.html?s_z=n_q_C25744&globalKeyword=C25744) | C25744 (https://www.lcsc.com/datasheet/C25744.pdf) | $ 0.0013 x 1
Resistor | MFET_GATE/3V3_FB | x2 | 22kΩ 62.5mW Thick Film Resistor ±1% | 0402 | C25768 | 0402WGF2202TCE | C25768 (https://www.lcsc.com/product-detail/C25768.html?s_z=n_q_C25768&globalKeyword=C25768) | C25768 (https://www.lcsc.com/datasheet/C25768.pdf) | $ 0.0010 x 1
Resistor | MFET_GATE/3V3_FB/STUSB_Reset | x3 | 100kΩ 62.5mW Thick Film Resistor ±1% | 0402 | C25741 | 0402WGF1003TCE | C25741 (https://www.lcsc.com/product-detail/C25741.html?s_z=n_q_C25741&globalKeyword=C25741) | C25741 (https://www.lcsc.com/datasheet/C25741.pdf) | $ 0.0009 x 1
Resistor | 3V3_Enable | x1 | 220kΩ 100mW Thick Film Resistor ±1% | 0603 | C22961 | 0603WAF2203T5E | C22961 (https://www.lcsc.com/product-detail/C22961.html?s_z=n_q_C22961&globalKeyword=C22961) | C22961 (https://www.lcsc.com/datasheet/C22961.pdf) | $ 0.0014 x 1
Resistor | 3V3_Enable | x1 | 510kΩ 100mW Thick Film Resistor ±1% | 0603 | C23192 | 0603WAF5103T5E | C23192 (https://www.lcsc.com/product-detail/C23192.html?s_z=n_q_C23192&globalKeyword=C23192) | C23192 (https://www.lcsc.com/datasheet/C23192.pdf) | $ 0.0019 x 1
Resistor | 3V3_Enable | x1 | 56kΩ 100mW Thick Film Resistor ±1% | 0603 | C23206 | 0603WAF5602T5E | C23206 (https://www.lcsc.com/product-detail/C23206.html?s_z=n_q_C23206&globalKeyword=C23206) | C23206 (https://www.lcsc.com/datasheet/C23206.pdf) | $ 0.0016 x 1
Inductor | BOOT | x1 | 10uH 2A | 1210 | C39846661 | XRTC322512S100MBCA | C39846661 (https://jlcpcb.com/partdetail/XR-XRTC322512S100MBCA/C39846661) | C39846661 (https://www.lcsc.com/datasheet/C39846661.pdf) | $0.1224 x 1
LED | Rød | x1 | 2.4V 20mA 40mW 615nm~630nm | 0603 | C2286 | KT-0603R | C2286 (https://jlcpcb.com/partdetail/Hubei_KENTOElec-KT0603R/C2286) | C2286 (https://jlcpcb.com/api/file/downloadByFileSystemAccessId/8550723991833485312) | $0.0064 x 1
LED | Grønn | x1 | 2.6V~3.1V 5mA 100mW 513nm~528nm | 0805 | C2297 | KT-0805G | C2297 (https://jlcpcb.com/parts/2nd/Optoelectronics/LED_Indication_Discrete_71) | C2297 (https://jlcpcb.com/api/file/downloadByFileSystemAccessId/8639582106239348736) | $0.0157 x 1
Connector | USB-C Connector | x2 | 20V 5A -30℃~+80℃ | 8.94mmx7.35mmx3.26mm | C165948 | TYPE-C-31-M-12 | C165948 (https://www.lcsc.com/product-detail/C165948.html?s_z=n_USB-C%2520connector) | C165948 (https://www.lcsc.com/datasheet/C165948.pdf) | $0.1810 x 1
Connector | OUTPUT | x1 | 3 Position Wire to Board Terminal Block | Through Hole 2.54mm | C49291873 | C254128V-3P0G36 | C49291873 (https://www.lcsc.com/product-detail/C49291873.html?s_z=n_q_C49291873&globalKeyword=C49291873) | C49291873 (https://www.lcsc.com/datasheet/C49291873.pdf) | $ 0.3968 x 1
Connector | DC power | x1 | 2 Position Wire to Board Terminal Block | Through Hole 2.54mm | C49291872 | C254128V-2P0G36 | C49291872 (https://www.lcsc.com/product-detail/C49291872.html?s_z=n_q_C49291872&globalKeyword=C49291872) | C49291872 (https://www.lcsc.com/datasheet/C49291872.pdf) | $ 0.2661 x 1
Switch | EN, BOOT | x2 | Black Round Button SMD | 4mmx3mmx2mm | C720477 | TS-1088-AR02016 | C720477 (https://jlcpcb.com/partdetail/XUNPU-TS_1088AR02016/C720477) | C720477 (https://jlcpcb.com/api/file/downloadByFileSystemAccessId/8588886944068096000) | $0.0555 x 1
IC | USB-C PD | x1 | 3V;5.5V 160uA -40℃~+105℃ | 2.6mmx2.6mmx0.5mm | C2678061 | STUSB4500QTR | C2678061 (https://www.lcsc.com/product-detail/C2678061.html?s_z=n_STUSB4500) | C2678061 (https://www.lcsc.com/datasheet/C2678061.pdf) | $1.3770 x 1
IC | Encoder | x1 | 3V~3.6V 7mA -40℃~+150℃ | 5mmx6mmx1.75mm | C2655191 | TLE5009E1000FUMA1 | C2655191 (https://www.lcsc.com/product-detail/C2655191.html?s_z=n_TLE5009E1000FUMA1%2520) | C2655191 (https://www.lcsc.com/datasheet/C2655191.pdf) | $3.7725 x 1
IC | Microcontroller | x1 | 2.4GHz 3V~3.6V 97mA -40℃~+85℃ | 20.5mmx15.4mmx2.4mm | C2913206 | ESP32-S3-MINI-1-N8 | C2913206 (https://www.lcsc.com/product-detail/C2913206.html?s_z=n_esp32-s3%2520wroom%25201) | C2913206 (https://www.lcsc.com/datasheet/C2913206.pdf) | $4.5968 x 1
IC | Motor driver | x1 | 4.5-35V 8A peak 200-kHz PWM -40℃~+125℃ | 5mmx7mmx1mm | C20345369 | DRV8316CRQRGFRQ1 | C20345369 (https://jlcpcb.com/partdetail/TexasInstruments-DRV8316CRQRGFRQ1/C20345369) | C20345369 (https://jlcpcb.com/api/file/downloadByFileSystemAccessId/8590902495441076224) | $6.6228 x 1
IC | Voltage regulator | x1 | 500kHz Buck Adjustable 2A 4.5V~28V | 1.6mmx2.9mmx1mm | C191884 | TPS54202DDCR | C191884 (https://www.lcsc.com/product-detail/C191884.html?s_z=n_TPS54202) | C191884 (https://www.lcsc.com/datasheet/C191884.pdf) | $0.2030 x 1
Mosfet | Power mosfet for power switching | x1 | 30V 40A | 3.15mmx3.3mmx0.75mm | C49452333 | STL9P3LLH6-TP | C49452333 (https://www.lcsc.com/product-detail/C49452333.html?s_z=n_STL9P3LLH6) | C49452333 (https://www.lcsc.com/datasheet/C49452333.pdf) | $0.1990 x 1
Diode | VCC buss diode | x3 | 30V 5A | 5mmx2.7mmx1mm | C50603 | PMEG3050EP,115 | C50603 (https://www.lcsc.com/product-detail/C50603.html?s_z=n_PMEG3050EP) | C50603 (https://www.lcsc.com/datasheet/C50603.pdf) | $0.4075 x 1
Diode | ESD Diode | x1 | 25VC Clamp ESD DIODE | 1.6mmx3mmx1.4mm | C95343 | ESDA25L | C95343 (https://www.lcsc.com/product-detail/C95343.html?s_z=n_ESDA25L) | C95343 (https://www.lcsc.com/datasheet/C95343.pdf) | $0.0826 x 1
Diode | ESD Diode | x3 | 38VC Clamp ESD DIODE | 1.6mmx1mmx0.5mm | C19829649 | ESDA25P35-1U1M | C19829649 (https://www.lcsc.com/product-detail/C19829649.html?s_z=n_ESDA25P35) | C19829649 (https://www.lcsc.com/datasheet/C19829649.pdf) | $0.1098 x 1

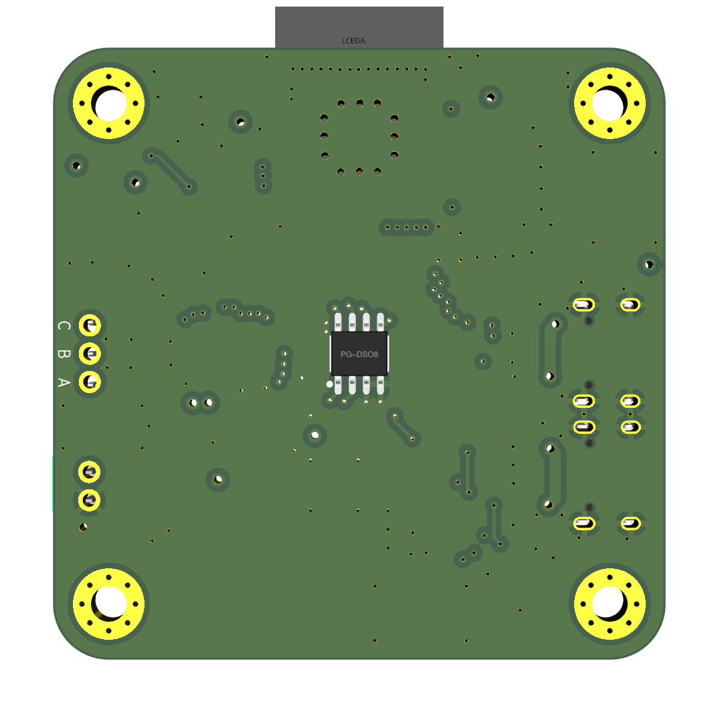
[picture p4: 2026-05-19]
Hardware/PCB_ComponentsBackCompressed.png

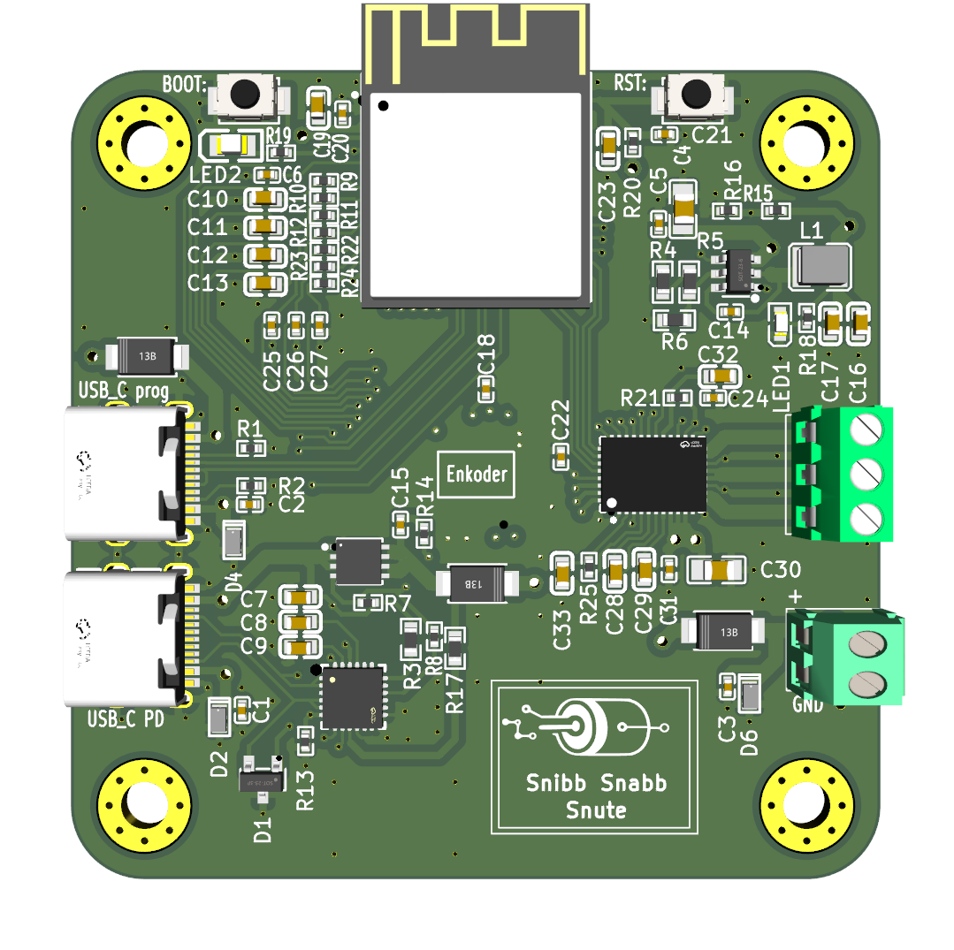
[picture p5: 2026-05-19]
Hardware/PCB_ComponentsFrontCompressed.png

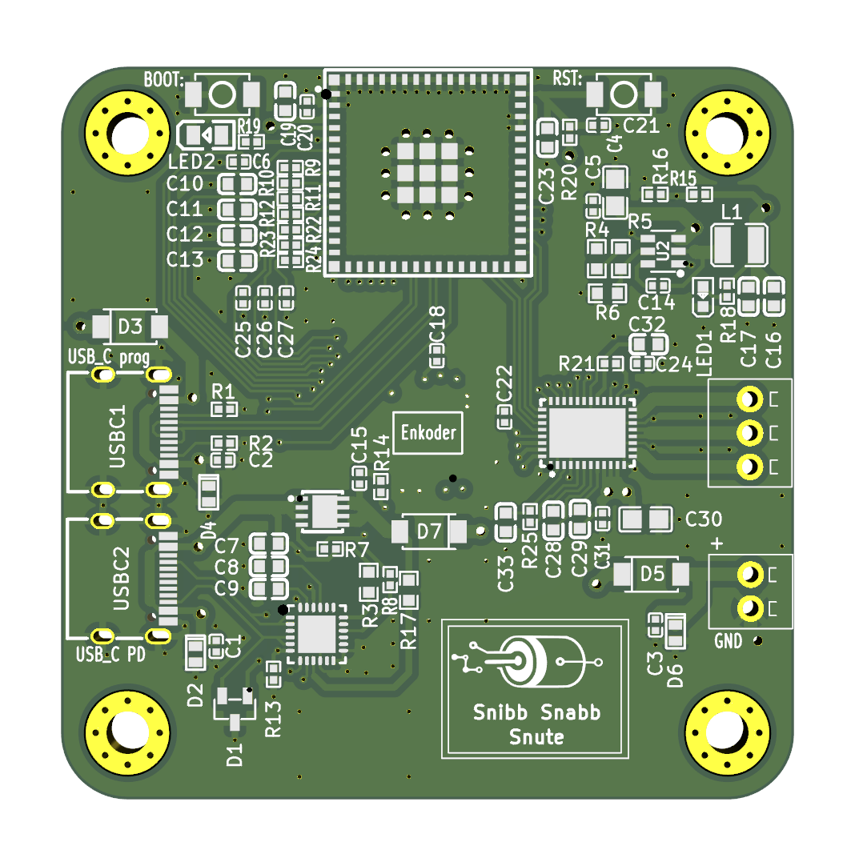
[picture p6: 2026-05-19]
Hardware/PCB_FrontComponents.png

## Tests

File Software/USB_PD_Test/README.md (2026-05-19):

# USB PD Test 
 
Test project for STUSB4500 USB Power Delivery controller. 
 
## Required Libraries: 
- **SparkFun_STUSB4500** - Install via Arduino Library Manager 
 
## Installation: 
1. Open Arduino IDE 
2. Go to **Sketch  Include Library  Manage Libraries** 
3. Search for "SparkFun STUSB4500" and install

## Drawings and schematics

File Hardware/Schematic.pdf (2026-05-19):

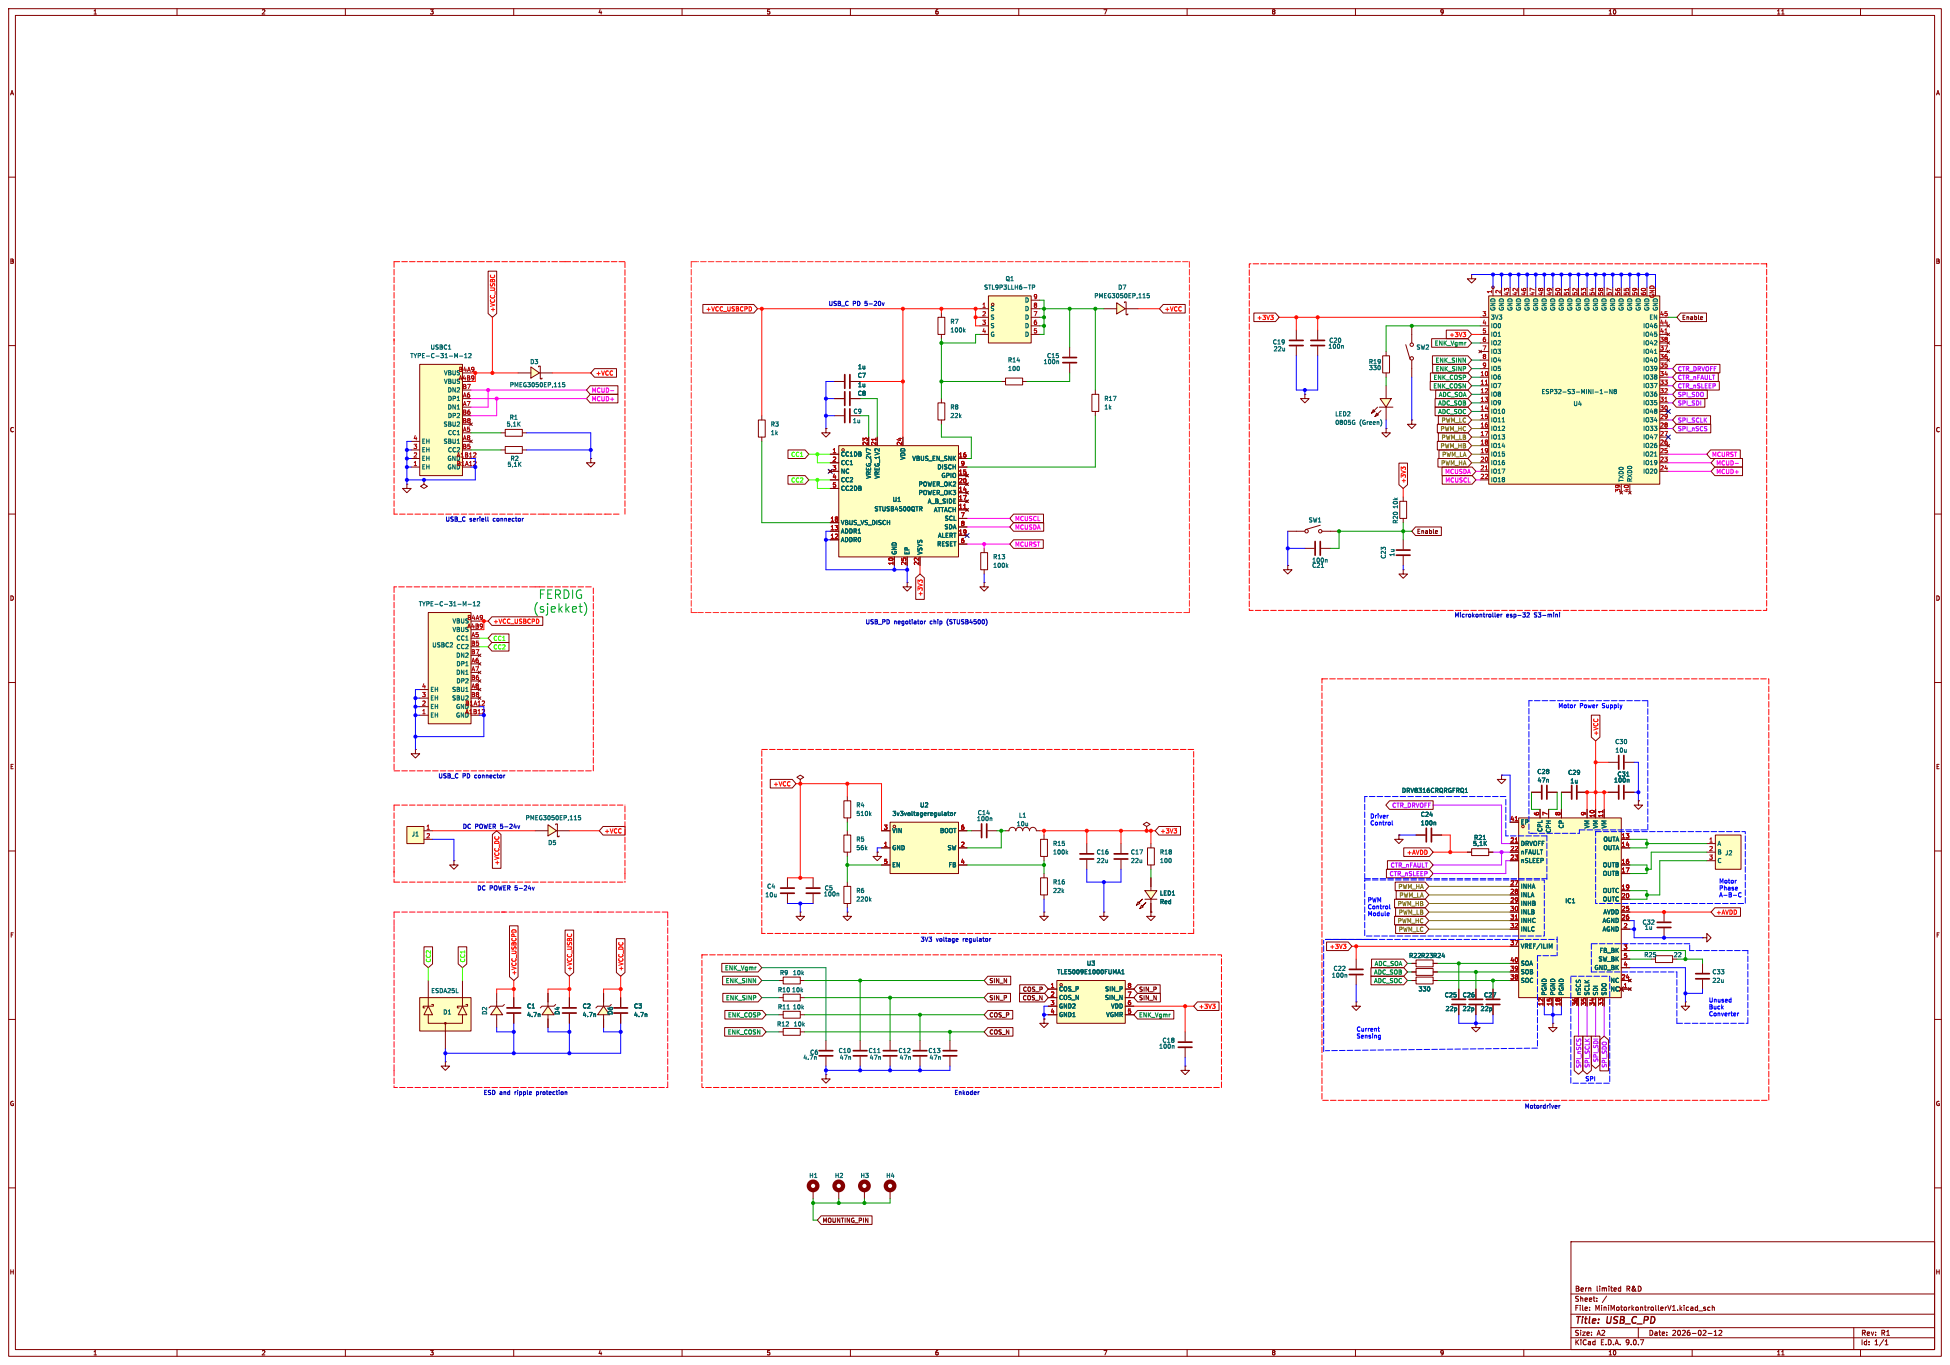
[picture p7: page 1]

2 GND 43 GND 42 GND 46 GND 47 GND 48 GND 49 GND 50 GND 51 GND 52 GND 53 GND 54 GND 58 GND 57 GND 56 TXD0 39 GND 55 RXD0 40 GND 59 GND 60 GNDGND
22 GND
PWM_LA MCUSCL +3V3
ENK_Vgmr

9 SCLK 35 VM 10 SDI 34 VM 11 SDO 33 OUTA

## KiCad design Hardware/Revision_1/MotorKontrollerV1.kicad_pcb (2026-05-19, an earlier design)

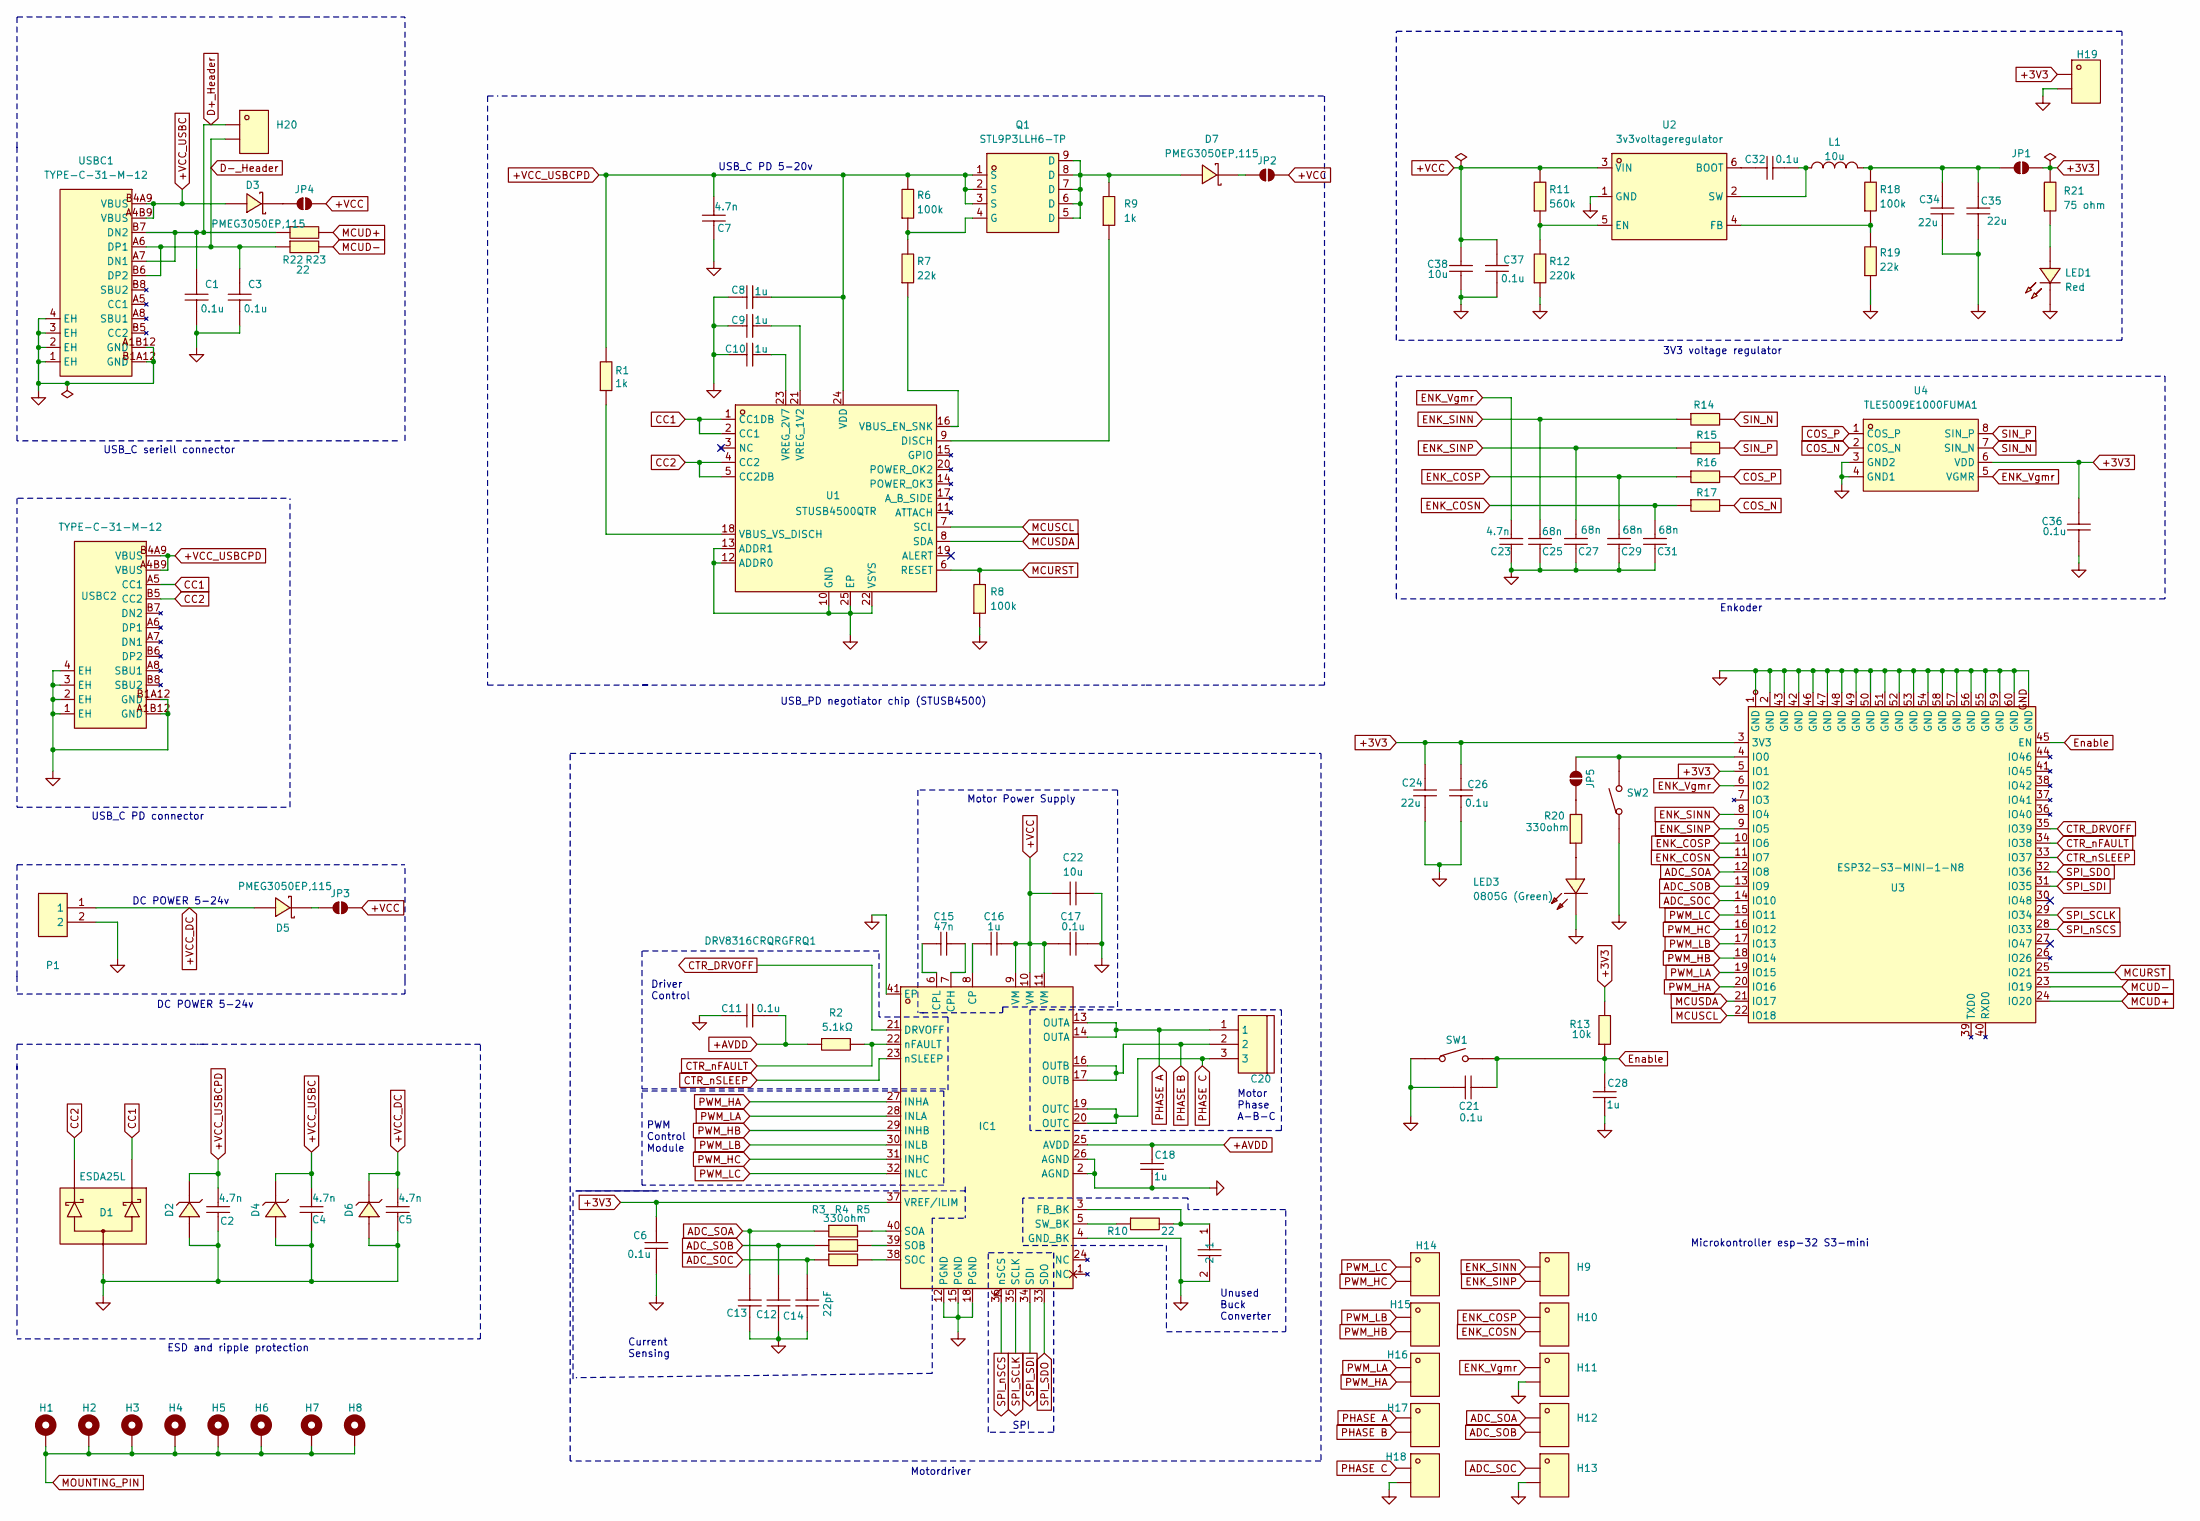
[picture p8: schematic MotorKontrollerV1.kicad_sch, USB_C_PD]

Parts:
C1, C3, C6, C11, C17, C21, C26, C32, C36, C37: 0.1u; C0603; LCSC Part C14663
C2, C4, C5, C7, C23: 4.7n; C0603; LCSC Part C53987
C8, C9, C10, C16, C18, C28: 1u; C0805; LCSC Part C28323
C12, C13, C14: 22pF; C0402; LCSC Part C1555
C15: 47n; C0603; LCSC Part C1622
C19, C24, C34, C35: 22u; C0805; LCSC Part C45783
C20: WJ500V-5.08-3P-14-00A; CONN-TH_3P-P5.00_WJ500V-5.08-3P; LCSC Part C72334
C22, C38: 10u; C1206; LCSC Part C13585
C25, C27, C29, C31: 68n; C1206; LCSC Part C77084
D1: ESDA25L; SOT-23-3_L2.9-W1.3-P1.90-LS2.4-BR; LCSC Part C95343
D2, D4, D6: ESDA25P35-1U1M_C19829649; DFN1610-2L_L1.6-W1.0-P1.10-RD; LCSC Part C19829649
D3, D5, D7: PMEG3050EP,115; SOD-128_L3.7-W2.5-LS4.7-RD; LCSC Part C50603
H1, H2, H3, H4, H5, H6, H7, H8: MountingHole_Pad_MP; MountingHole_3.2mm_M3_Pad_Via
H9, H10, H11, H12, H13, H14, H15, H16, H17, H18, H19, H20: PZ254V-11-02P; HDR-TH_2P-P2.54-V-M; LCSC Part C492401
IC1: DRV8316CRQRGFRQ1; VQFN-40_L7.0-W5.0-P0.50-BL-EP5.7; LCSC Part C20345369
JP1, JP2, JP3, JP4, JP5: SolderJumper_2_Open; SolderJumper-2_P1.3mm_Open_RoundedPad1.0x1.5mm
L1: 10u; IND-SMD_L3.2-W2.5_CKST322512-2.2UH; LCSC Part C39846661
LED1: Red; LED0603-RD_RED; LCSC Part C2286
LED3: 0805G (Green); LED0805-R-RD; LCSC Part C2297
P1: WJ500V-5.08-2P-14-00A; CONN-TH_2P-P5.00_WJ500V-5.08-2P; LCSC Part C8465
Q1: STL9P3LLH6-TP; DFN-8_L3.0-W3.0-P0.65-BL_WPM3028-8; LCSC Part C49452333
R1, R9: 1k; R0805; LCSC Part C17513
R2: 5.1kΩ; R0402; LCSC Part C25905
R3, R4, R5, R20: 330ohm; R0805; LCSC Part C17630
R6, R8, R18: 100k; R0805_NEW; LCSC Part C149504
R7, R19: 22k; R0805; LCSC Part C17560
R10, R22, R23: 22; R0805; LCSC Part C17561
R11: 560k; R0805; LCSC Part C15785
R12: 220k; R0805; LCSC Part C17556
R13, R14, R15, R16, R17: 10k; R0603; LCSC Part C25804
R21: 75 ohm; R0603; LCSC Part C4275
SW1, SW2: TS-1088-AR02016; SW-SMD_L3.9-W3.0-P4.45; LCSC Part C720477
U1: STUSB4500QTR; QFN-24_L4.0-W4.0-P0.50-BL-EP2.8; LCSC Part C2678061
U2: 3v3voltageregulator; SOT-23-6_L2.9-W1.6-P0.95-LS2.8-BL; LCSC Part C191884
U3: ESP32-S3-MINI-1-N8; BULETM-SMD_ESP32-S3-MINI-1-N8; LCSC Part C2913206
U4: TLE5009E1000FUMA1; PG-DSO-8_L5.0-W4.0-P1.27-LS6.0-BL; LCSC Part C2655191
USBC1, USBC2: TYPE-C-31-M-12; USB-C_SMD-TYPE-C-31-M-12_1; LCSC Part C165948

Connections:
+3V3: C6.1, C24.1, C26.2, C36.2, H19.1, IC1.37 (VREF/ILIM), JP1.2 (B), R13.2, R21.2, U3.3 (3V3), U3.5 (IO1), U4.6 (VDD)
+AVDD: C11.2, C18.2, IC1.25 (AVDD), R2.1
+VCC: C16.1, C17.1, C22.1, C37.2, C38.2, IC1.9 (VM), IC1.10 (VM), IC1.11 (VM), JP2.2 (B), JP3.2 (B), JP4.2 (B), R11.2, U2.3 (VIN)
+VCC_DC: C5.2, D5.2 (A), D6.1 (C), P1.1
+VCC_USBC: C4.2, D3.2 (A), D4.1 (C), USBC1.A4B9 (VBUS), USBC1.B4A9 (VBUS)
+VCC_USBCPD: C2.2, C7.2, C8.1, D2.1 (C), Q1.1 (S), Q1.2 (S), Q1.3 (S), R1.2, R6.2, U1.24 (VDD), USBC2.A4B9 (VBUS), USBC2.B4A9 (VBUS)
ADC_SOA: C12.2, H12.1, R3.1, U3.12 (IO8)
ADC_SOB: C13.2, H12.2, R4.1, U3.13 (IO9)
ADC_SOC: C14.2, H13.1, R5.1, U3.14 (IO10)
CC1: D1.1, U1.1 (CC1DB), U1.2 (CC1), USBC2.A5 (CC1)
CC2: D1.2, U1.4 (CC2), U1.5 (CC2DB), USBC2.B5 (CC2)
COS_N: R17.2, U4.2 (COS_N)
COS_P: R16.2, U4.1 (COS_P)
CTR_DRVOFF: IC1.21 (DRVOFF), U3.35 (IO39)
CTR_nFAULT: IC1.22 (nFAULT), R2.2, U3.34 (IO38)
CTR_nSLEEP: IC1.23 (nSLEEP), U3.33 (IO37)
D+_Header: C1.1, H20.1, R22.1, USBC1.A7 (DN1), USBC1.B7 (DN2)
D-_Header: C3.1, H20.2, R23.1, USBC1.A6 (DP1), USBC1.B6 (DP2)
ENK_COSN: C31.2, H10.2, R17.1, U3.11 (IO7)
ENK_COSP: C29.2, H10.1, R16.1, U3.10 (IO6)
ENK_SINN: C25.2, H9.1, R14.1, U3.8 (IO4)
ENK_SINP: C27.2, H9.2, R15.1, U3.9 (IO5)
ENK_Vgmr: C23.2, H11.1, U3.6 (IO2), U4.5 (VGMR)
Enable: C21.1, C28.2, R13.1, SW1.2, U3.45 (EN)
GND: C1.2, C2.1, C3.2, C4.1, C5.1, C6.2, C7.1, C8.2, C9.2, C10.2, C11.1, C12.1, C13.1, C14.1, C17.2, C18.1, C19.2, C21.2, C22.2, C23.1, C24.2, C25.1, C26.1, C27.1, C28.1, C29.1, C31.1, C34.2, C35.2, C36.1, C37.1, C38.1, D1.3, D2.2 (A), D4.2 (A), D6.2 (A), H11.2, H13.2, H18.2, H19.2, IC1.2 (AGND), IC1.4 (GND_BK), IC1.12 (PGND), IC1.15 (PGND), IC1.18 (PGND), IC1.26 (AGND), IC1.41 (EP), LED1.1 (K), LED3.2 (K), P1.2, R8.1, R12.1, R19.1, SW1.1, SW2.1, U1.10 (GND), U1.12 (ADDR0), U1.13 (ADDR1), U1.22 (VSYS), U1.25 (EP), U2.1 (GND), U3.1 (GND), U3.2 (GND), U3.42 (GND), U3.43 (GND), U3.46 (GND), U3.47 (GND), U3.48 (GND), U3.49 (GND), U3.50 (GND), U3.51 (GND), U3.52 (GND), U3.53 (GND), U3.54 (GND), U3.55 (GND), U3.56 (GND), U3.57 (GND), U3.58 (GND), U3.59 (GND), U3.60 (GND), U3.GND, U4.3 (GND2), U4.4 (GND1), USBC1.1 (EH), USBC1.2 (EH), USBC1.3 (EH), USBC1.4 (EH), USBC1.A1B12 (GND), USBC1.B1A12 (GND), USBC2.1 (EH), USBC2.2 (EH), USBC2.3 (EH), USBC2.4 (EH), USBC2.A1B12 (GND), USBC2.B1A12 (GND)
MCUD+: R22.2, U3.24 (IO20)
MCUD-: R23.2, U3.23 (IO19)
MCURST: R8.2, U1.6 (RESET), U3.25 (IO21)
MCUSCL: U1.7 (SCL), U3.22 (IO18)
MCUSDA: U1.8 (SDA), U3.21 (IO17)
MOUNTING_PIN: H1.1 (MP), H2.1 (MP), H3.1 (MP), H4.1 (MP), H5.1 (MP), H6.1 (MP), H7.1 (MP), H8.1 (MP)
unnamed: D3.1 (K), JP4.1 (A)
unnamed: D5.1 (K), JP3.1 (A)
unnamed: D7.2 (A), Q1.5 (D), Q1.6 (D), Q1.7 (D), Q1.8 (D), Q1.9 (D), R9.2
unnamed: D7.1 (K), JP2.1 (A)
unnamed: C16.2, IC1.8 (CP)
unnamed: C15.2, IC1.7 (CPH)
unnamed: C15.1, IC1.6 (CPL)
unnamed: C19.1, IC1.3 (FB_BK), R10.2
unnamed: IC1.40 (SOA), R3.2
unnamed: IC1.39 (SOB), R4.2
unnamed: IC1.38 (SOC), R5.2
unnamed: IC1.5 (SW_BK), R10.1
unnamed: C34.1, C35.1, JP1.1 (A), L1.2, R18.2
unnamed: JP5.1 (A), SW2.2, U3.4 (IO0)
unnamed: JP5.2 (B), R20.2
unnamed: LED1.2 (A), R21.1
unnamed: LED3.1 (A), R20.1
unnamed: Q1.4 (G), R6.1, R7.2
unnamed: R9.1, U1.9 (DISCH)
unnamed: R7.1, U1.16 (VBUS_EN_SNK)
unnamed: R1.1, U1.18 (VBUS_VS_DISCH)
unnamed: C9.1, U1.21 (VREG_1V2)
unnamed: C10.1, U1.23 (VREG_2V7)
unnamed: C32.2, U2.6 (BOOT)
unnamed: R11.1, R12.2, U2.5 (EN)
unnamed: R18.1, R19.2, U2.4 (FB)
unnamed: C32.1, L1.1, U2.2 (SW)
PHASE A: C20.1, H17.1, IC1.13 (OUTA), IC1.14 (OUTA)
PHASE B: C20.2, H17.2, IC1.16 (OUTB), IC1.17 (OUTB)
PHASE C: C20.3, H18.1, IC1.19 (OUTC), IC1.20 (OUTC)
PWM_HA: H16.2, IC1.27 (INHA), U3.20 (IO16)
PWM_HB: H15.2, IC1.29 (INHB), U3.18 (IO14)
PWM_HC: H14.2, IC1.31 (INHC), U3.16 (IO12)
PWM_LA: H16.1, IC1.28 (INLA), U3.19 (IO15)
PWM_LB: H15.1, IC1.30 (INLB), U3.17 (IO13)
PWM_LC: H14.1, IC1.32 (INLC), U3.15 (IO11)
SIN_N: R14.2, U4.7 (SIN_N)
SIN_P: R15.2, U4.8 (SIN_P)
SPI_SCLK: IC1.35 (SCLK), U3.29 (IO34)
SPI_SDI: IC1.34 (SDI), U3.31 (IO35)
SPI_SDO: IC1.33 (SDO), U3.32 (IO36)
SPI_nSCS: IC1.36 (nSCS), U3.28 (IO33)

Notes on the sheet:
Motor Power Supply
Motor Phase A-B-C
Driver Control
USB_C PD 5-20v
PWM Control Module
SPI
Current Sensing
3V3 voltage regulator
Microkontroller esp-32 S3-mini
USB_C PD connector
DC POWER 5-24v
USB_C seriell connector
Unused Buck Converter
Enkoder
Motordriver
ESD and ripple protection
USB_PD negotiator chip (STUSB4500)

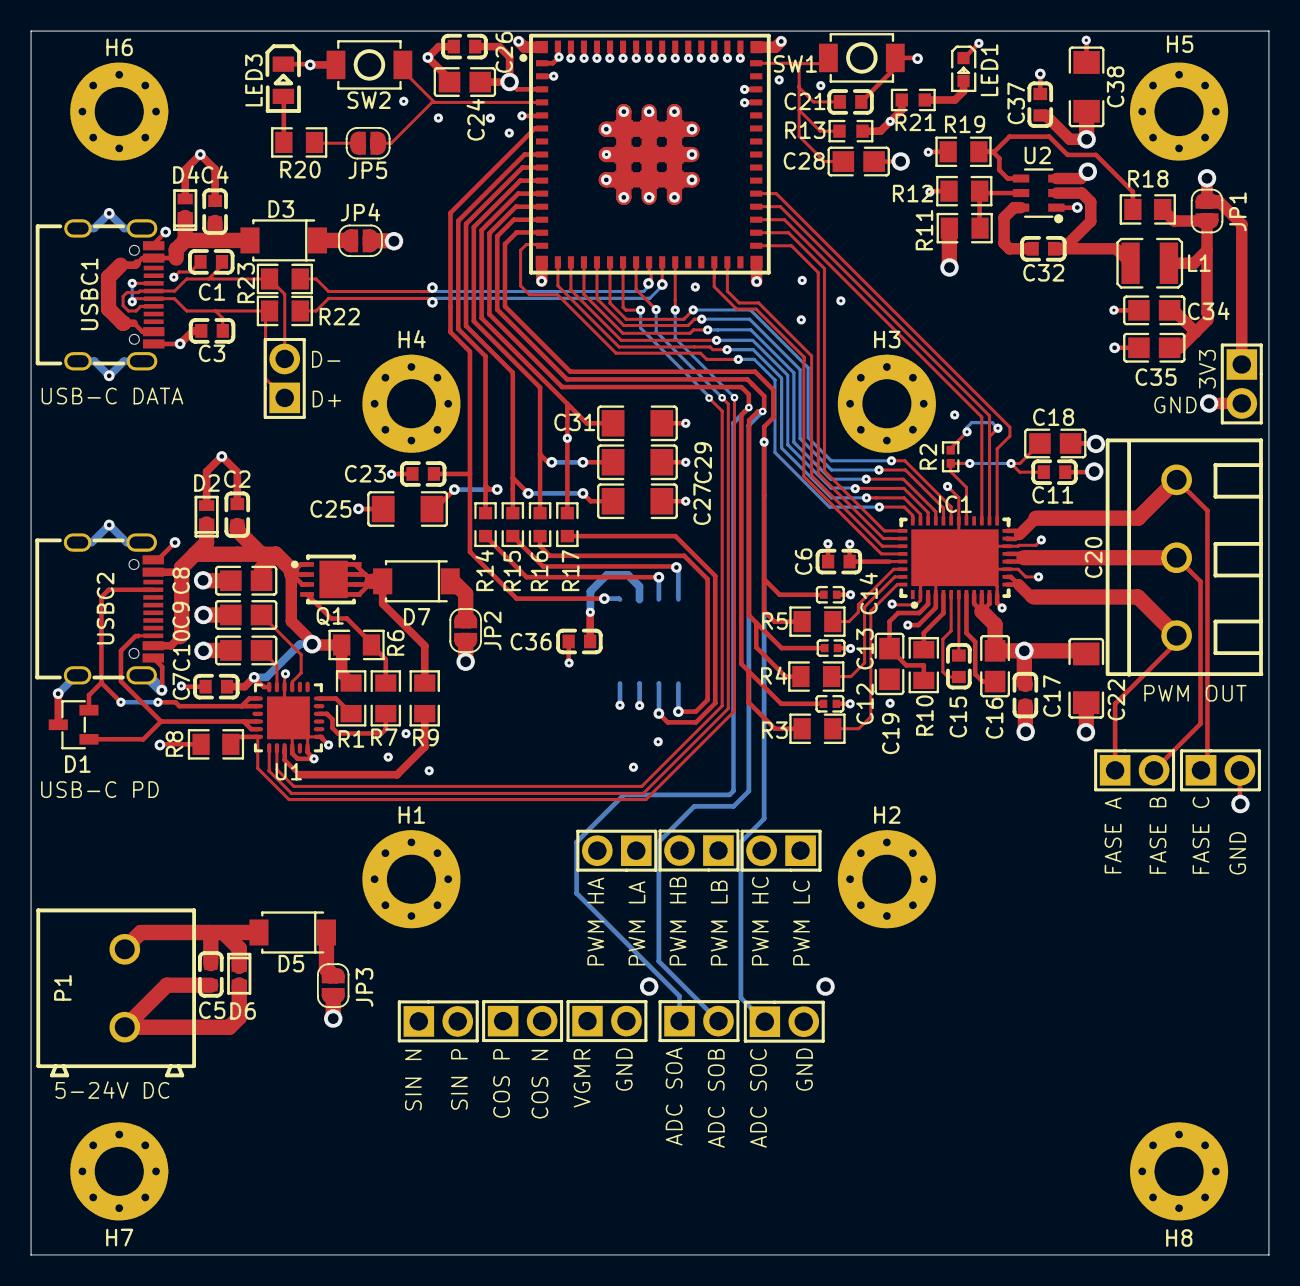
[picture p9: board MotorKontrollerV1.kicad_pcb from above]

Board: 6 copper layers, 80.7 x 79.8 mm, 105 parts (1 on the bottom side), 73 nets.

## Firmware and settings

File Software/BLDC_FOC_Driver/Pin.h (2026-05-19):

#ifndef PIN_H
#define PIN_H

namespace Pin 
{

    //**        ADC PINS            **//
    const uint8_t MC_Vref = 1;
    const uint8_t ENK_Vgmr = 2;
    const uint8_t ENK_SinN = 4;
    const uint8_t ENK_SinP = 5;
    const uint8_t ENK_CosP = 6;
    const uint8_t ENK_CosN = 7;
    const uint8_t MC_SOA = 8;
    const uint8_t MC_SOB = 9;
    const uint8_t MC_SOC = 10;


    //**        PWM PINS            **//    
    const uint8_t PWM_LC = 11;
    const uint8_t PWM_HC = 12;
    const uint8_t PWM_LB = 13;
    const uint8_t PWM_HB = 14;
    const uint8_t PWM_LA = 15;
    const uint8_t PWM_HA = 16;


    //**        I2C PINS            **//    
    const uint8_t I2C_SDA = 17;
    const uint8_t I2C_SCL = 18;


    //**        D PINS              **//    
    const uint8_t DPluss = 19;
    const uint8_t DMinus = 20;


    //**        SPI/FLAG PINS       **//
    const uint8_t PDA_RST = 21;
    const uint8_t SPI_nSCS = 33;
    const uint8_t SPI_SCLK = 34;
    const uint8_t SPI_SDI = 35;
    const uint8_t SPI_SDO = 36;
    const uint8_t MC_nSLEEP = 37;
    const uint8_t MC_nFAULT = 38;
    const uint8_t MC_DRVOFF = 39;
    
}

#endif 

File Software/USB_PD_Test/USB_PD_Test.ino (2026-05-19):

#include <Wire.h>
#include <SparkFun_STUSB4500.h>

#define SDA_PIN 17
#define SCL_PIN 18

STUSB4500 usb;

// ================================================================
// TEST VOLTAGES - cycles through these every second
// ================================================================
const float voltages[] = {5.0, 9.0, 15.0, 20.0};
const int numVoltages = 4;
int currentIdx = 0;

unsigned long lastSwitch = 0;
const unsigned long switchInterval = 1000;  // 1 second

void setup() {
    Serial.begin(115200);
    delay(1000);
    Serial.println("\nSTUSB4500 Voltage Test Bench");
    Serial.println("============================");

    // ========== Init I2C and STUSB4500 ==========
    Wire.begin(SDA_PIN, SCL_PIN);
    delay(500);

    if (!usb.begin()) {
        Serial.println("Could not find STUSB4500!");
        while (1);
    }
    Serial.println("STUSB4500 connected!");

    // ========== Configure 3 PDOs ==========
    // PDO1 is FIXED at 5V (USB-PD specification requirement)
    // PDO2 and PDO3 are programmable

    usb.setPdoNumber(3);    

    // PDO1: 5V (fixed by spec, but set current)
    usb.setCurrent(1, 3.0);

    // PDO2: 9V
    usb.setVoltage(2, 9.0);
    usb.setCurrent(2, 3.0);

    // PDO3: starts at 15V (we'll change between 15V and 20V at runtime)
    usb.setVoltage(3, 15.0);
    usb.setCurrent(3, 3.0);

    usb.write();   
    usb.softReset();
    delay(100);

    Serial.println("PDOs configured:");
    Serial.printf("  PDO1: %.1fV (fixed)\n", usb.getVoltage(1));
    Serial.printf("  PDO2: %.1fV\n",        usb.getVoltage(2));
    Serial.printf("  PDO3: %.1fV\n",        usb.getVoltage(3));
    Serial.println("\nStarting voltage cycle...\n");
}

void loop() {
    if (millis() - lastSwitch >= switchInterval) {
        float targetVoltage = voltages[currentIdx];

        // ========== Select correct PDO based on voltage ==========
        if (targetVoltage == 5.0) {
            usb.setPdoNumber(1);  // PDO1 = 5V
        }
        else if (targetVoltage == 9.0) {
            usb.setPdoNumber(2);  // PDO2 = 9V
        }
        else {
            // For 15V or 20V, reprogram PDO3 and select it
            usb.setVoltage(3, targetVoltage);
            usb.setPdoNumber(3);
        }
        // Trigger renegotiation
        usb.softReset();

        uint8_t activePDO = usb.getPdoNumber();

        Serial.printf("PDO %d : %.0fV\n", activePDO, targetVoltage);
        // Move to next voltage in cycle
        currentIdx = (currentIdx + 1) % numVoltages;
        lastSwitch = millis();
    }
}

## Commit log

2026-05-19 Legg til BLDC_FOC_Driver og USB_PD_Test prosjekt
2026-05-19 Legg til Fusion360 CAD-filer (.f3z)
2026-05-19 Add component list (PDF and Excel)
    [Oversikt over komponenter.xlsx]
2026-05-19 Add PNG images to CAD folder
2026-05-19 Added hardware-files for revision1 and revision2 of the board
    [BOM-MiniMotorkontrollerV1.csv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]
2026-05-19 Added Pinout File
    [ESP32_S3_Mini_Pinout.xlsx]
2026-05-19 Added PDF of the schematic
2026-05-19 Added the 3d models of the PCB
